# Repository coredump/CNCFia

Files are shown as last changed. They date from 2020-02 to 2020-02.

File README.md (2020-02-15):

# CNCFia

The idea with this board is to provide a *generic* shield/daughter card for 3.3V MCUs running CNC firmwares like GRBL (and its ports) and g2core. For that, instead of making a shield with specific sockets, we decided to provide a pin header that can be used to connect to different MCUs.

## Included capabilities

### Switches

There are six opto-isolated connectors for limit switches (X, Y, and Z Min/Max limits), a Probe connector and an extra opto-isolated connector to be used for any generic function, and five non-opto isolated ones to be used for external controls (Door security, Emergency Stop, etc).

The opto-isolated switches have an option to be powered by an entirely separated power source to provide full electrical isolation.

All the switches are pulled UP via 4.7kΩ resistors, intended to be used with NC (normally closed) switches connected to the GND, making it an active low signal. Take that in consideration when wiring/configuring the software.

### External driver control/level shifting

Support for nine voltage shifted outputs, mosfet (2n700X) driven. Enough to provide Step/Pulse/Enable signals for three external drivers (those usually have a 5V control voltage).

The mosfets connect the outputs to GND, so when wiring make sure to provide the 5V common wire to all positive (+) signals and the outputs to the negative (-) signals.

TODO example

## Jumper Settings

|  JP1  | Result |
| :---: | --- |
|  1-2  | 5V voltage for board functions will be provided by external power source connected to **EXTERNAL 5V IN** |
|  1-3  | 5V to board functions will be provided by the MCU 5V Pin connected to the controller input |

## Connector Descriptions

TODO add descriptions and image

## Electrical notes

View this project on [CADLAB.io](https://cadlab.io/project/2459).

All calculations were made considering a 3.3V output from the driving MCU pins, while keeping the output currents under 10 mA, what should be safe for most of the MCUs around.

The 3904s driving the relays have a base current (Ib) of ~ 7.8 mA, that should be enough to saturate the transistor and provide the 78 mA needed by the relay coil.

The LTV-847s are used with typical values for Vf and If, according to datasheet specs.

The OPAMP output for the spindle can be regulated with a potentiometer and from the 3.3V PWM it can get values close to 11V with a 12V power source. Simulated circuit shows a 0.4s approximately time to get to the stable voltage.

## License, Copyright and disclaimers

Copyright Jose Junior <jose.junior@gmail.com> 2020.  

This documentation describes Open Hardware and is licensed under the
CERN OHL v. 1.2.  

You may redistribute and modify this documentation under the terms of the
[CERN OHL v.1.2.](http://ohwr.org/cernohl) This documentation is distributed
**WITHOUT ANY EXPRESS OR IMPLIED WARRANTY, INCLUDING OF
MERCHANTABILITY, SATISFACTORY QUALITY AND FITNESS FOR A
PARTICULAR PURPOSE**. Please see the CERN OHL v.1.2 for applicable
conditions.

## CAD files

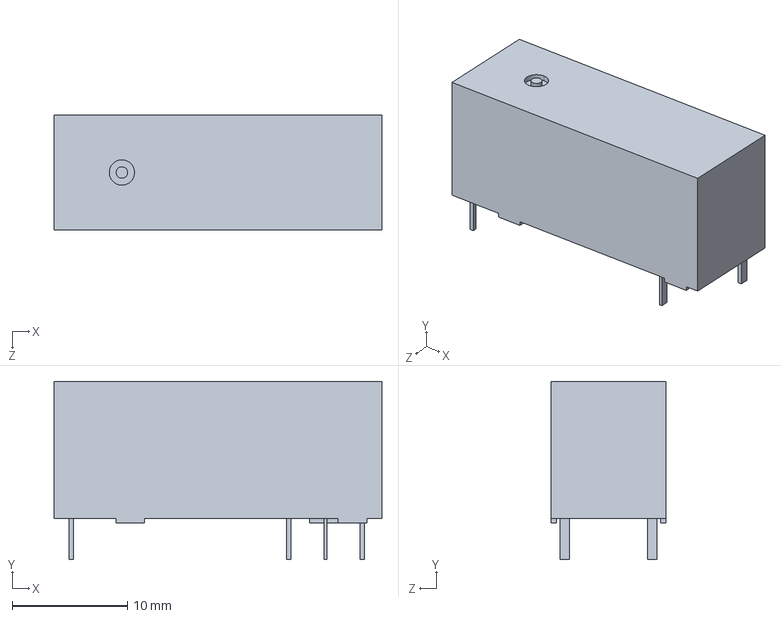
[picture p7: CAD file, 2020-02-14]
Custom/Kicad_extra_3d/G6RL_1.step
28.5 x 15.5 x 10.0 mm

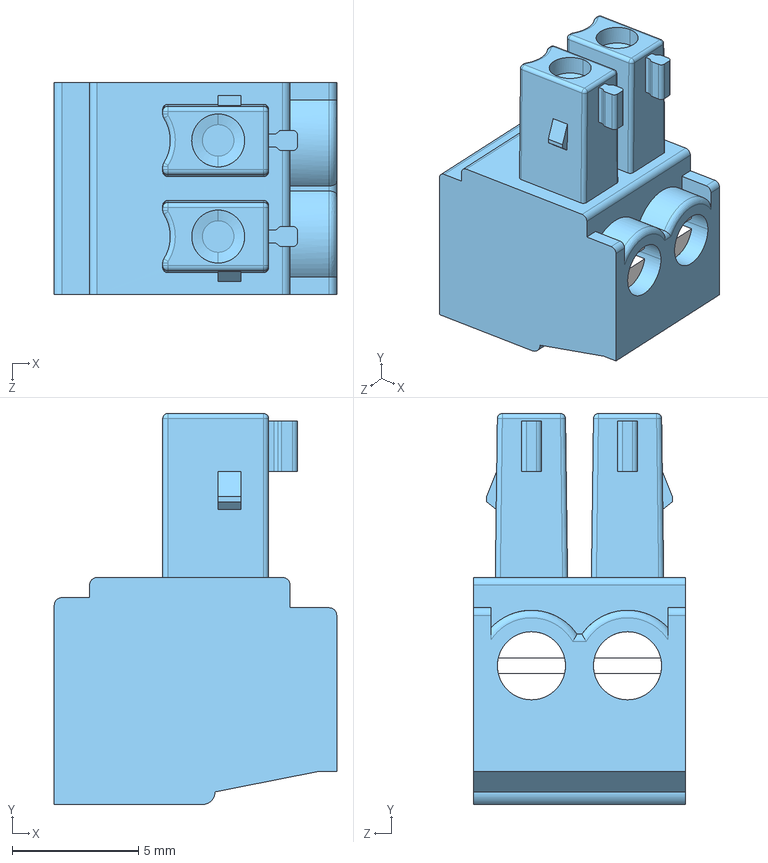
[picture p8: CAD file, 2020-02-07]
Custom/Kicad_extra_3d/CUI_DEVICES_TBP02P1-381-02BE.step
11.2 x 15.5 x 8.41 mm

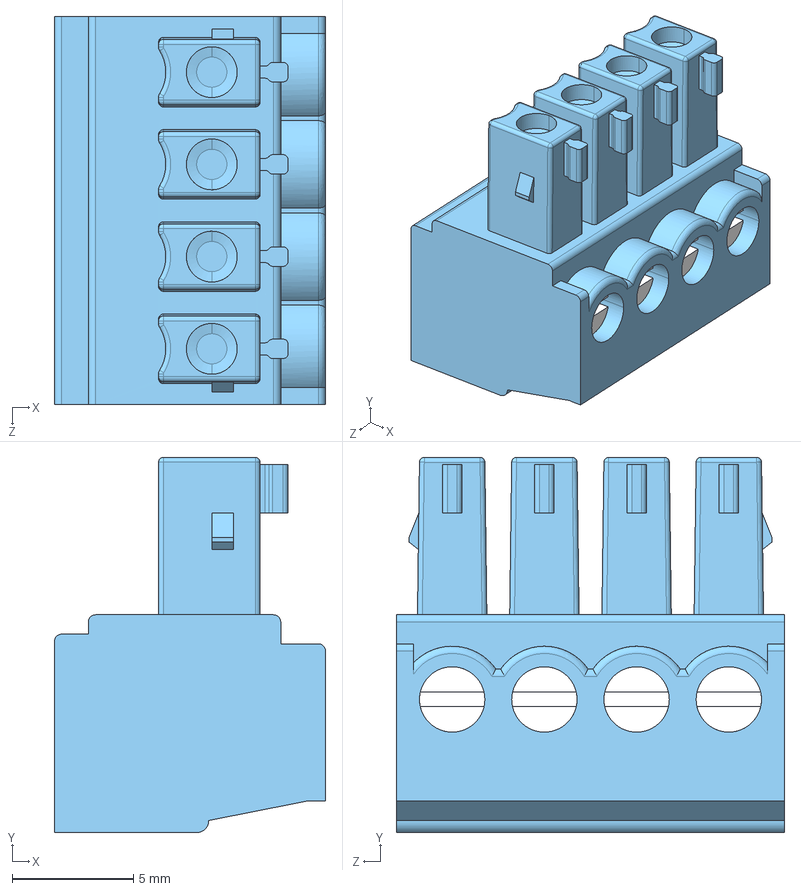
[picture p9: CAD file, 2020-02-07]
Custom/Kicad_extra_3d/CUI_DEVICES_TBP02P1-381-04BE.step
11.2 x 15.5 x 16.0 mm

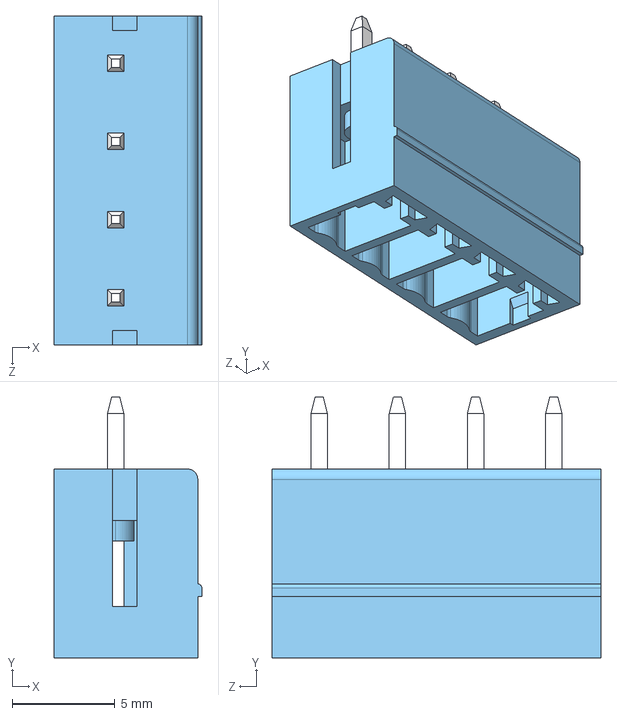
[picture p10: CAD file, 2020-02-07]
Custom/Kicad_extra_3d/CUI_DEVICES_TBP02R2-381-04BE.step
7.20 x 12.7 x 16.0 mm

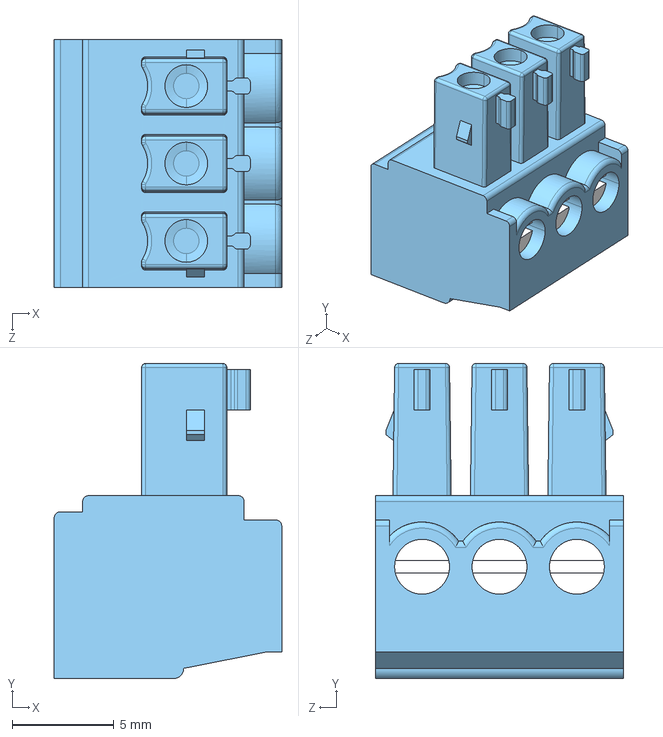
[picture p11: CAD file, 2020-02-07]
Custom/Kicad_extra_3d/CUI_DEVICES_TBP02P1-381-03BE.step
11.2 x 15.5 x 12.2 mm

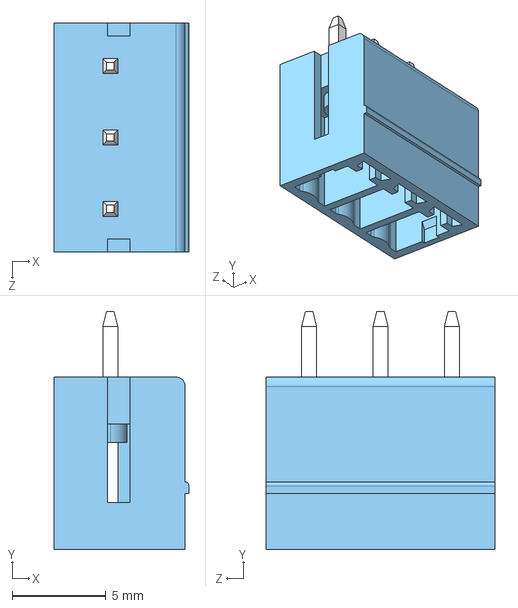
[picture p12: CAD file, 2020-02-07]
Custom/Kicad_extra_3d/CUI_DEVICES_TBP02R2-381-03BE.step
7.20 x 12.7 x 12.2 mm

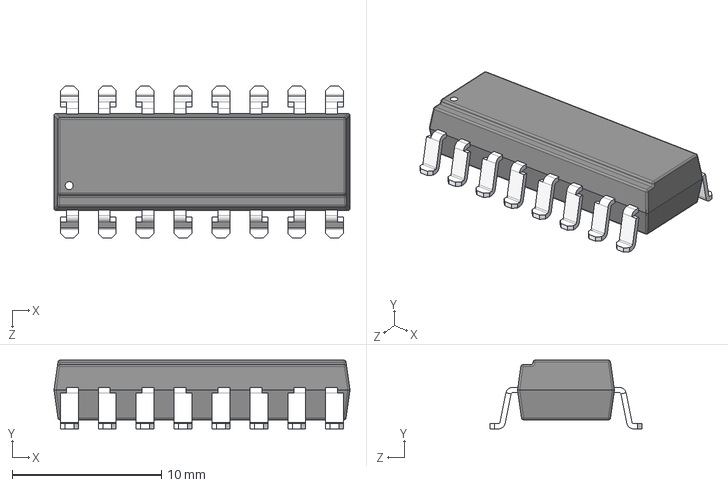
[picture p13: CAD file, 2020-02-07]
Custom/Kicad_extra_3d/LTV-846S--3DModel-STEP-56544.STEP
19.8 x 4.60 x 10.2 mm

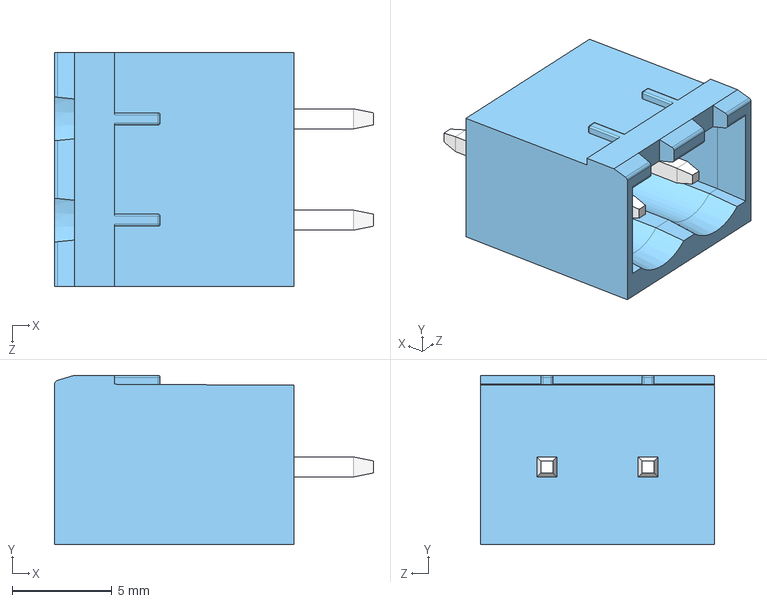
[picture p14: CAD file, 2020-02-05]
Custom/Kicad_extra_3d/CUI_DEVICES_TBP01R2-508-02BE.step
16.0 x 8.50 x 11.8 mm

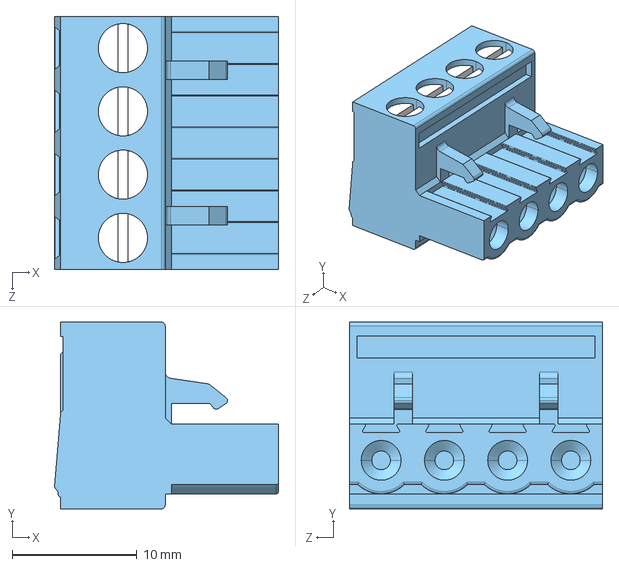
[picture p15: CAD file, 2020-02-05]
Custom/Kicad_extra_3d/CUI_DEVICES_TBP01P1-508-04BE.step
18.0 x 15.0 x 20.3 mm

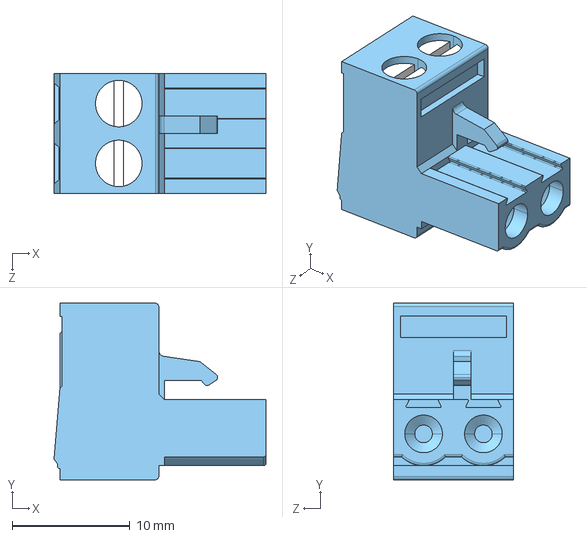
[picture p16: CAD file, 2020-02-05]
Custom/Kicad_extra_3d/CUI_DEVICES_TBP01P1-508-02BE.step
18.0 x 15.0 x 10.2 mm

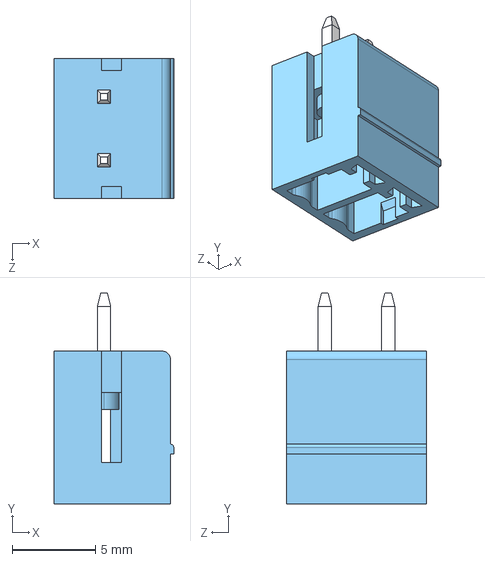
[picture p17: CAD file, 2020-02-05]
Custom/Kicad_extra_3d/CUI_DEVICES_TBP02R2-381-02BE.step
7.20 x 12.7 x 8.41 mm

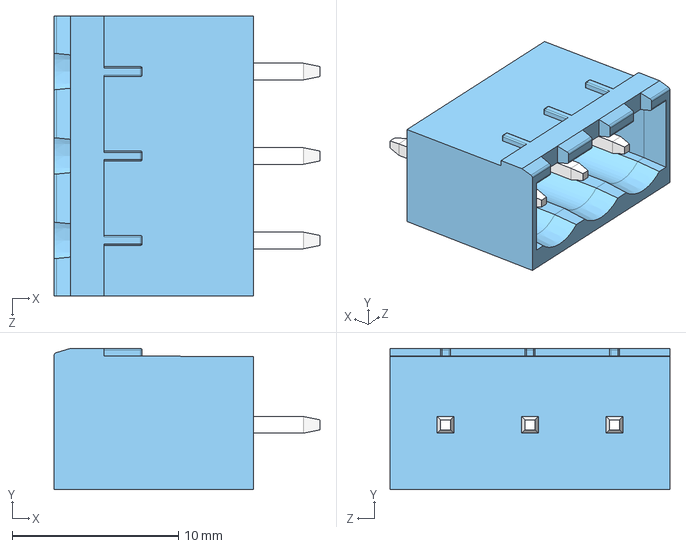
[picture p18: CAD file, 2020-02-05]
Custom/Kicad_extra_3d/CUI_DEVICES_TBP01R2-508-03BE.step
16.0 x 8.50 x 16.8 mm

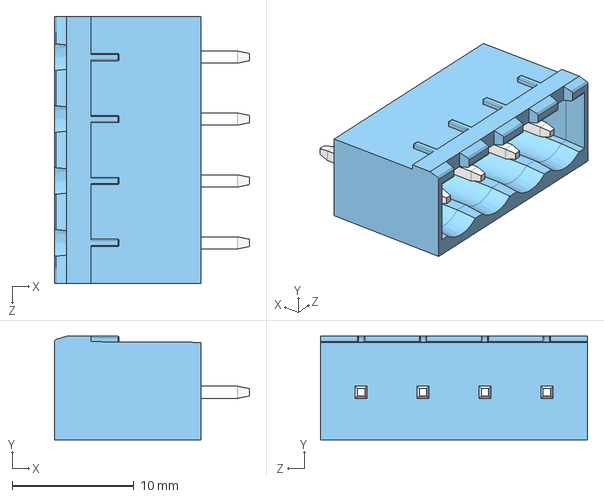
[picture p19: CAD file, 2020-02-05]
Custom/Kicad_extra_3d/CUI_DEVICES_TBP01R2-508-04BE.step
16.0 x 8.50 x 21.9 mm

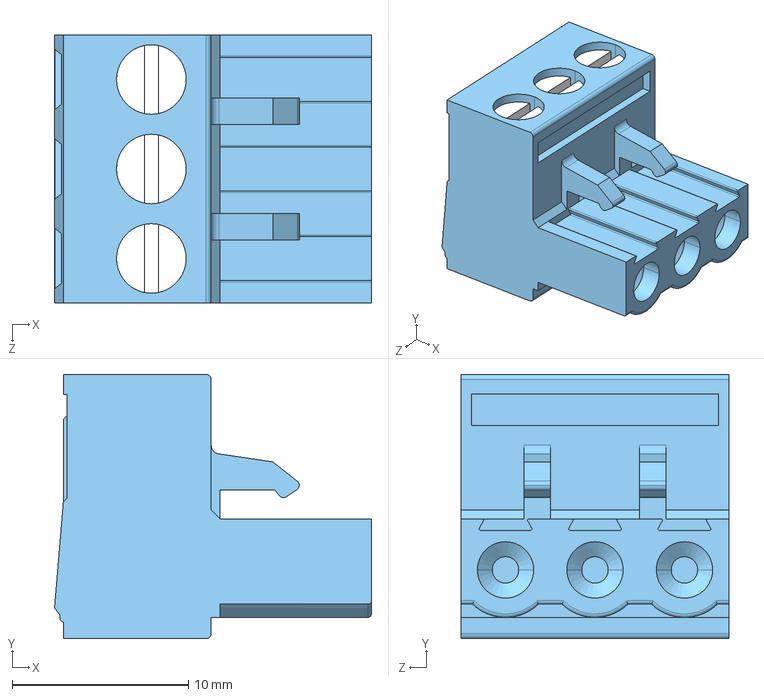
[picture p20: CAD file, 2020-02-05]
Custom/Kicad_extra_3d/CUI_DEVICES_TBP01P1-508-03BE.step
18.0 x 15.0 x 15.2 mm

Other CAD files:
Custom/Kicad_extra_3d/Omron Single.stp

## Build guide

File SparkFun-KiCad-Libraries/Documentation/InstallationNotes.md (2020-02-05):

Installation Notes
----------------

* [The KiCad site](http://kicad-pcb.org/)

**KiCad installation**

* Uninstall previous versions of KiCad
* Download KiCad stable version 4.0.5 from [http://kicad-pcb.org/download/](http://kicad-pcb.org/download/windows/) and install
* After install, you'll be prompted to install "Wings 3D", check this box to be redirected to [http://www.wings3d.com/](http://www.wings3d.com/)
* Download and install the stable release 2.1.5

**Using the libraries**

* Create a local project (this is necessary because projects hold library path information)
* Open the "Schematic Library Editor"
* Prefrences -> Component Libraries
  * Remove all libraries from list
  * Add -> navigate to SparkFun-KiCad-Libraries -> select all .lib files -> open, then hit OK
  * Test by selecting an active library.  All sparkfun libraries should be displayed.  Close the library editor
* Open the "PCB Footprint Editor"
* Preferences -> Footprint Library Manager
  * Remove all (if any) libraries, hit OK
* Preferences -> Footprint Libraries Wizard
  * Next (files on my computer)
  * Navigate to SparkFun-KiCad-Libraries -> select all .mod files and hit ok
  * Next
  * Select for this project only
  * Next
  * Close the editor
* Save the project (Green arrow into extern HDD icon, no menu exists)

Now, this project is linked to the libraries.  Open a schematic and place components.  See KiCad enginursday post for converting from schematic into board (Note: You need to have nets for this to work... not just unconnected components)

**License Information**

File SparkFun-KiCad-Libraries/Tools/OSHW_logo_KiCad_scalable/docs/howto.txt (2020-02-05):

How to make your own:
---------------------

Watch / read this first:

* http://www.kicad-pcb.org/display/KICAD/Videos+by+zupnikal

The last two videos should be helpful for how to create a custom .emp file from images.

* http://www.re-innovation.co.uk/web12/index.php/en/blog-75/230-adding-logo-to-kicad

If you use linux (which you should), you don't have to use the online-scaler. Just use the scripts!

---

* Create a folder to hold your new footprint library.
* Copy the scripts 'make_lib.sh' and 'scale.pl' into that folder.
* Make sure these files are executable (chmod u+x ...).
* Copy your custom .emp file into that foler.

* Run the 'make_lib.sh' script as follows:

./make_lib.sh input-file.emp lib-name.mod START END

START and END are placeholders for positive integer numbers (1,2,3...) that determine
the range of created footprint sizes. The units are metric (mm).

The 'lib-name.mod' file will show up in the 'lib' sub-folder. Add it to your pcbnew
library settings as usual.

Footprints that are created for back-layers are automagically mirrored horizontally.
To place them onto a back-layer, hover the mouse-pointer over them and press 'f' for 'flip'.

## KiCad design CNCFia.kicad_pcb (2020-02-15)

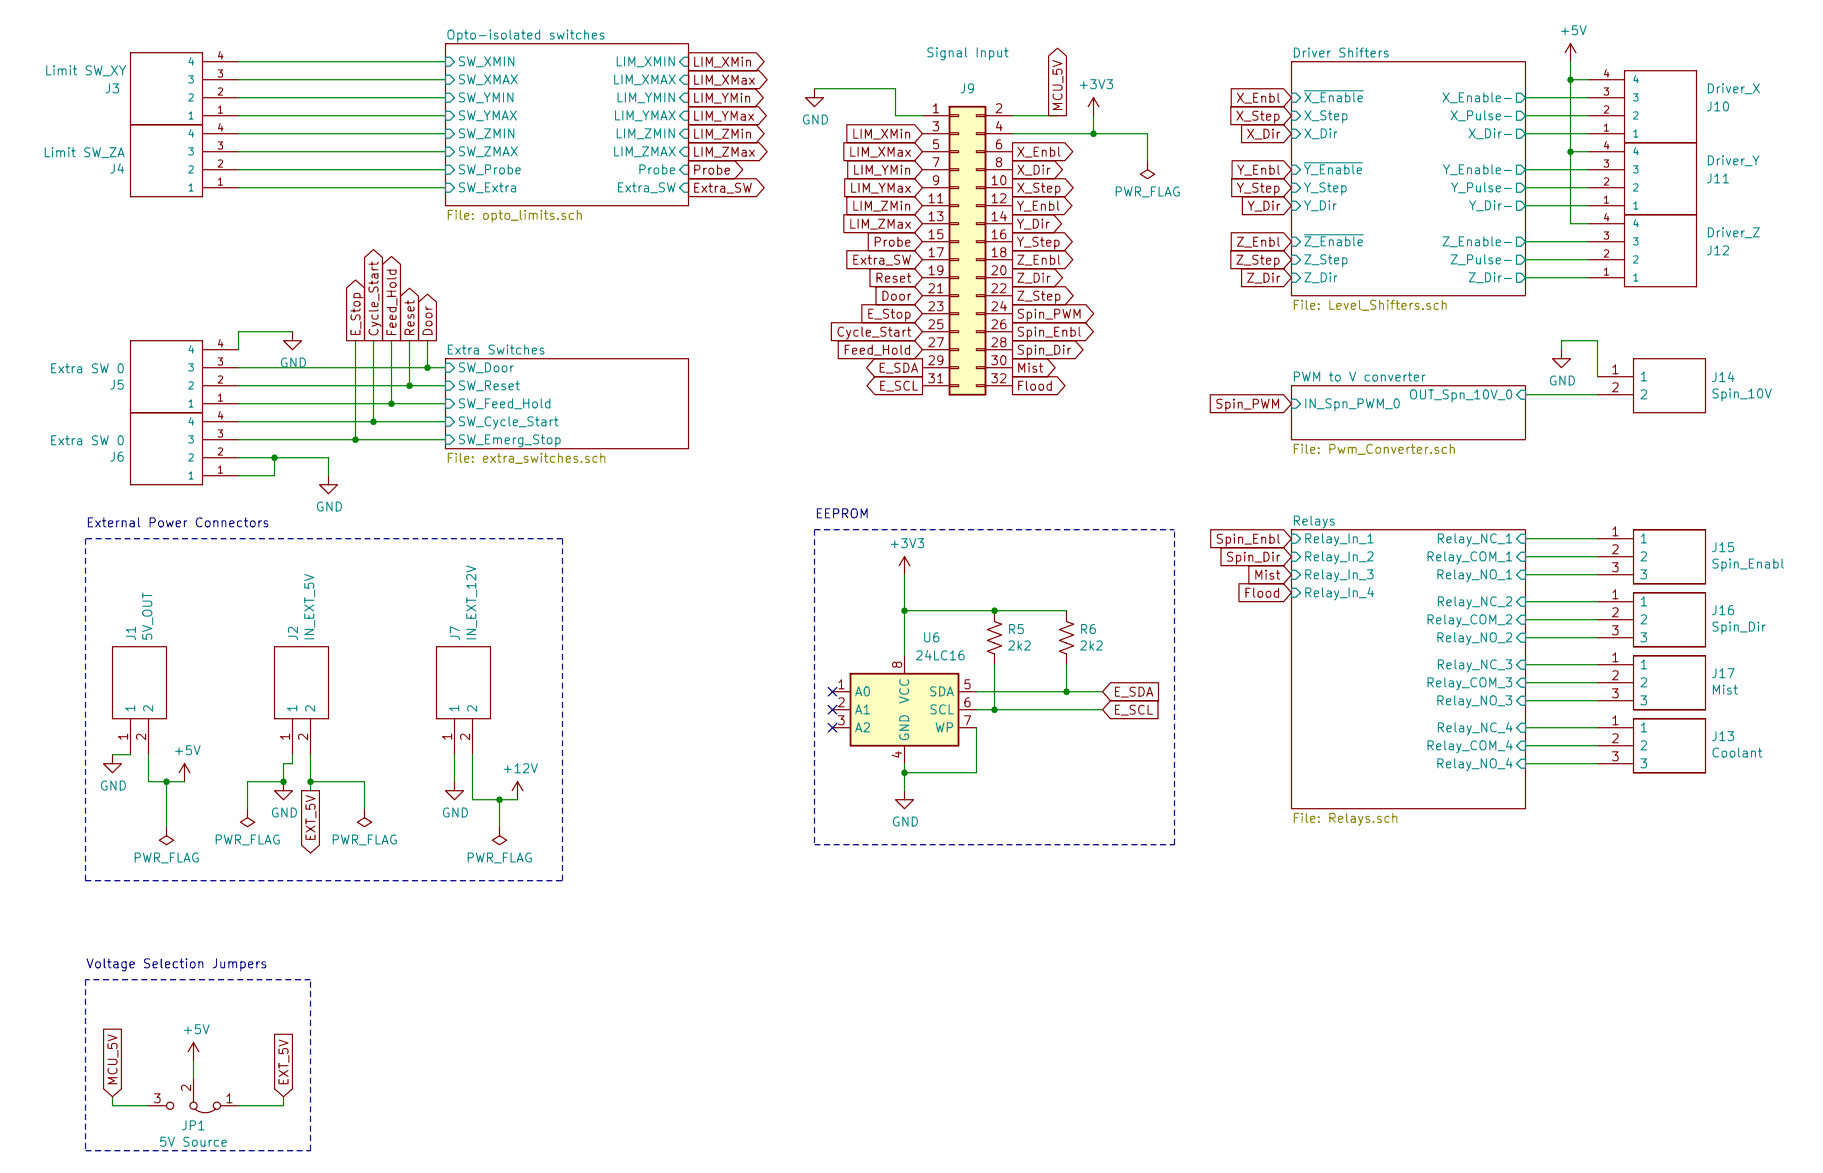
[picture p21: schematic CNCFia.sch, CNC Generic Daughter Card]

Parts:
J1: 5V_OUT; CUI_TBP02R2-381-02BE; Mouser Part Number 490-TB008A-508-02BE
J2: IN_EXT_5V; CUI_TBP02R2-381-02BE; Mouser Part Number 490-TB008A-508-02BE
J3: Limit SW_XY; CUI_TBP02R2-381-04BE; MPN TBP01R2-508-04BE; Digi-Key_PN 102-6424-ND
J4: Limit SW_ZA; CUI_TBP02R2-381-04BE; MPN TBP01R2-508-04BE; Digi-Key_PN 102-6424-ND
J5, J6: Extra SW 0; CUI_TBP02R2-381-04BE; MPN TBP01R2-508-04BE; Digi-Key_PN 102-6424-ND
J7: IN_EXT_12V; CUI_TBP02R2-381-02BE; Mouser Part Number 490-TB008A-508-02BE
J9: Signal Input; PinHeader_2x16_P2.54mm_Vertical; MPN 302-S401; Digi-Key_PN ED10529-ND
J10: Driver_X; CUI_TBP02R2-381-04BE; Mouser Part Number 490-TB008A-508-03BE
J11: Driver_Y; CUI_TBP02R2-381-04BE; Mouser Part Number 490-TB008A-508-03BE
J12: Driver_Z; CUI_TBP02R2-381-04BE; Mouser Part Number 490-TB008A-508-03BE
J13: Coolant; CUI_TBP02R2-381-03BE; Mouser Part Number 490-TB008A-508-03BE
J14: Spin_10V; CUI_TBP02R2-381-02BE; Mouser Part Number 490-TB008A-508-02BE
J15: Spin_Enabl; CUI_TBP02R2-381-03BE; Mouser Part Number 490-TB008A-508-03BE
J16: Spin_Dir; CUI_TBP02R2-381-03BE; Mouser Part Number 490-TB008A-508-03BE
J17: Mist; CUI_TBP02R2-381-03BE; Mouser Part Number 490-TB008A-508-03BE
JP1: 5V Source; PinHeader_1x03_P2.54mm_Vertical
R5, R6: 2k2; R_0805_2012Metric_Pad1.15x1.40mm_HandSolder; MPN CRGCQ1206F2K2; Digi-Key_PN A129814CT-ND
U6: 24LC16; SOIC-8_3.9x4.9mm_P1.27mm

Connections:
+3V3: J9.4, R5.1, R6.1, U6.8 (VCC); also elsewhere on the board
+5V: J1.2, J10.4, J11.4, J12.4, JP1.2 (C); also elsewhere on the board
+12V: J7.2; also elsewhere on the board
/OUT_Spn_10V_0: J14.2; also elsewhere on the board
/Relay_COM_1: J15.2; also elsewhere on the board
/Relay_COM_2: J16.2; also elsewhere on the board
/Relay_COM_3: J17.2; also elsewhere on the board
/Relay_COM_4: J13.2; also elsewhere on the board
/Relay_NC_1: J15.1; also elsewhere on the board
/Relay_NC_2: J16.1; also elsewhere on the board
/Relay_NC_3: J17.1; also elsewhere on the board
/Relay_NC_4: J13.1; also elsewhere on the board
/Relay_NO_1: J15.3; also elsewhere on the board
/Relay_NO_2: J16.3; also elsewhere on the board
/Relay_NO_3: J17.3; also elsewhere on the board
/Relay_NO_4: J13.3; also elsewhere on the board
/SW_Extra: J4.1; also elsewhere on the board
/SW_Probe: J4.2; also elsewhere on the board
/SW_XMAX: J3.3; also elsewhere on the board
/SW_XMIN: J3.4; also elsewhere on the board
/SW_YMAX: J3.1; also elsewhere on the board
/SW_YMIN: J3.2; also elsewhere on the board
/SW_ZMAX: J4.3; also elsewhere on the board
/SW_ZMIN: J4.4; also elsewhere on the board
/X_Dir-: J10.1; also elsewhere on the board
/X_Enable-: J10.3; also elsewhere on the board
/X_Pulse-: J10.2; also elsewhere on the board
/Y_Dir-: J11.1; also elsewhere on the board
/Y_Enable-: J11.3; also elsewhere on the board
/Y_Pulse-: J11.2; also elsewhere on the board
/Z_Dir-: J12.1; also elsewhere on the board
/Z_Enable-: J12.3; also elsewhere on the board
/Z_Pulse-: J12.2; also elsewhere on the board
Cycle_Start: J6.4, J9.25; also elsewhere on the board
Door: J5.3, J9.21; also elsewhere on the board
EXT_5V: J2.2, JP1.1 (A)
E_SCL: J9.31, R5.2, U6.6 (SCL)
E_SDA: J9.29, R6.2, U6.5 (SDA)
E_Stop: J6.3, J9.23; also elsewhere on the board
Extra_SW: J9.17; also elsewhere on the board
Feed_Hold: J5.1, J9.27; also elsewhere on the board
Flood: J9.32; also elsewhere on the board
GND: J1.1, J2.1, J5.4, J6.1, J6.2, J7.1, J9.1, J14.1, U6.4 (GND), U6.7 (WP); also elsewhere on the board
LIM_XMax: J9.5; also elsewhere on the board
LIM_XMin: J9.3; also elsewhere on the board
LIM_YMax: J9.9; also elsewhere on the board
LIM_YMin: J9.7; also elsewhere on the board
LIM_ZMax: J9.13; also elsewhere on the board
LIM_ZMin: J9.11; also elsewhere on the board
MCU_5V: J9.2, JP1.3 (B)
Mist: J9.30; also elsewhere on the board
Probe: J9.15; also elsewhere on the board
Reset: J5.2, J9.19; also elsewhere on the board
Spin_Dir: J9.28; also elsewhere on the board
Spin_Enbl: J9.26; also elsewhere on the board
Spin_PWM: J9.24; also elsewhere on the board
X_Dir: J9.8; also elsewhere on the board
X_Enbl: J9.6; also elsewhere on the board
X_Step: J9.10; also elsewhere on the board
Y_Dir: J9.14; also elsewhere on the board
Y_Enbl: J9.12; also elsewhere on the board
Y_Step: J9.16; also elsewhere on the board
Z_Dir: J9.20; also elsewhere on the board
Z_Enbl: J9.18; also elsewhere on the board
Z_Step: J9.22; also elsewhere on the board

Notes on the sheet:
External Power Connectors
Voltage Selection Jumpers
EEPROM

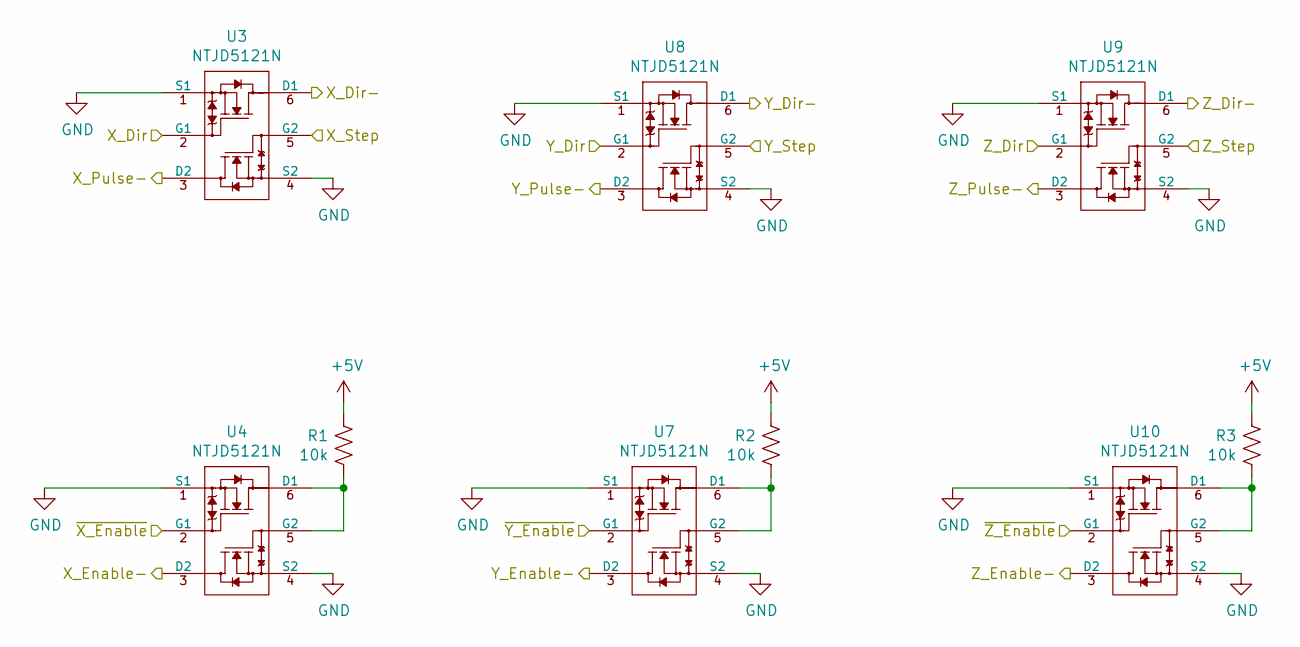
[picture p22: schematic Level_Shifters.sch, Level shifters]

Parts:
R1, R2, R3: 10k; R_0805_2012Metric_Pad1.15x1.40mm_HandSolder
U3, U4, U7, U8, U9, U10: NTJD5121N; SOT-363_SC-70-6

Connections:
+5V: R1.1, R2.1, R3.1; also elsewhere on the board
/X_Dir-: U3.6 (D1); also elsewhere on the board
/X_Enable-: U4.3 (D2); also elsewhere on the board
/X_Pulse-: U3.3 (D2); also elsewhere on the board
/Y_Dir-: U8.6 (D1); also elsewhere on the board
/Y_Enable-: U7.3 (D2); also elsewhere on the board
/Y_Pulse-: U8.3 (D2); also elsewhere on the board
/Z_Dir-: U9.6 (D1); also elsewhere on the board
/Z_Enable-: U10.3 (D2); also elsewhere on the board
/Z_Pulse-: U9.3 (D2); also elsewhere on the board
GND: U3.1 (S1), U3.4 (S2), U4.1 (S1), U4.4 (S2), U7.1 (S1), U7.4 (S2), U8.1 (S1), U8.4 (S2), U9.1 (S1), U9.4 (S2), U10.1 (S1), U10.4 (S2); also elsewhere on the board
unnamed: R1.2, U4.5 (G2), U4.6 (D1)
unnamed: R2.2, U7.5 (G2), U7.6 (D1)
unnamed: R3.2, U10.5 (G2), U10.6 (D1)
X_Dir: U3.2 (G1); also elsewhere on the board
X_Enbl: U4.2 (G1); also elsewhere on the board
X_Step: U3.5 (G2); also elsewhere on the board
Y_Dir: U8.2 (G1); also elsewhere on the board
Y_Enbl: U7.2 (G1); also elsewhere on the board
Y_Step: U8.5 (G2); also elsewhere on the board
Z_Dir: U9.2 (G1); also elsewhere on the board
Z_Enbl: U10.2 (G1); also elsewhere on the board
Z_Step: U9.5 (G2); also elsewhere on the board

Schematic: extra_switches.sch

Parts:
RN3: CAY17-472JALF; RESCAXS64P320X160X60-10N; MPN CAY17-472JALF; Digi-Key_PN CAY17-472JALFCT-ND

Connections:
+3V3: RN3.5, RN3.10; also elsewhere on the board
Cycle_Start: RN3.2; also elsewhere on the board
Door: RN3.6; also elsewhere on the board
E_Stop: RN3.1; also elsewhere on the board
Feed_Hold: RN3.3; also elsewhere on the board
Reset: RN3.4; also elsewhere on the board

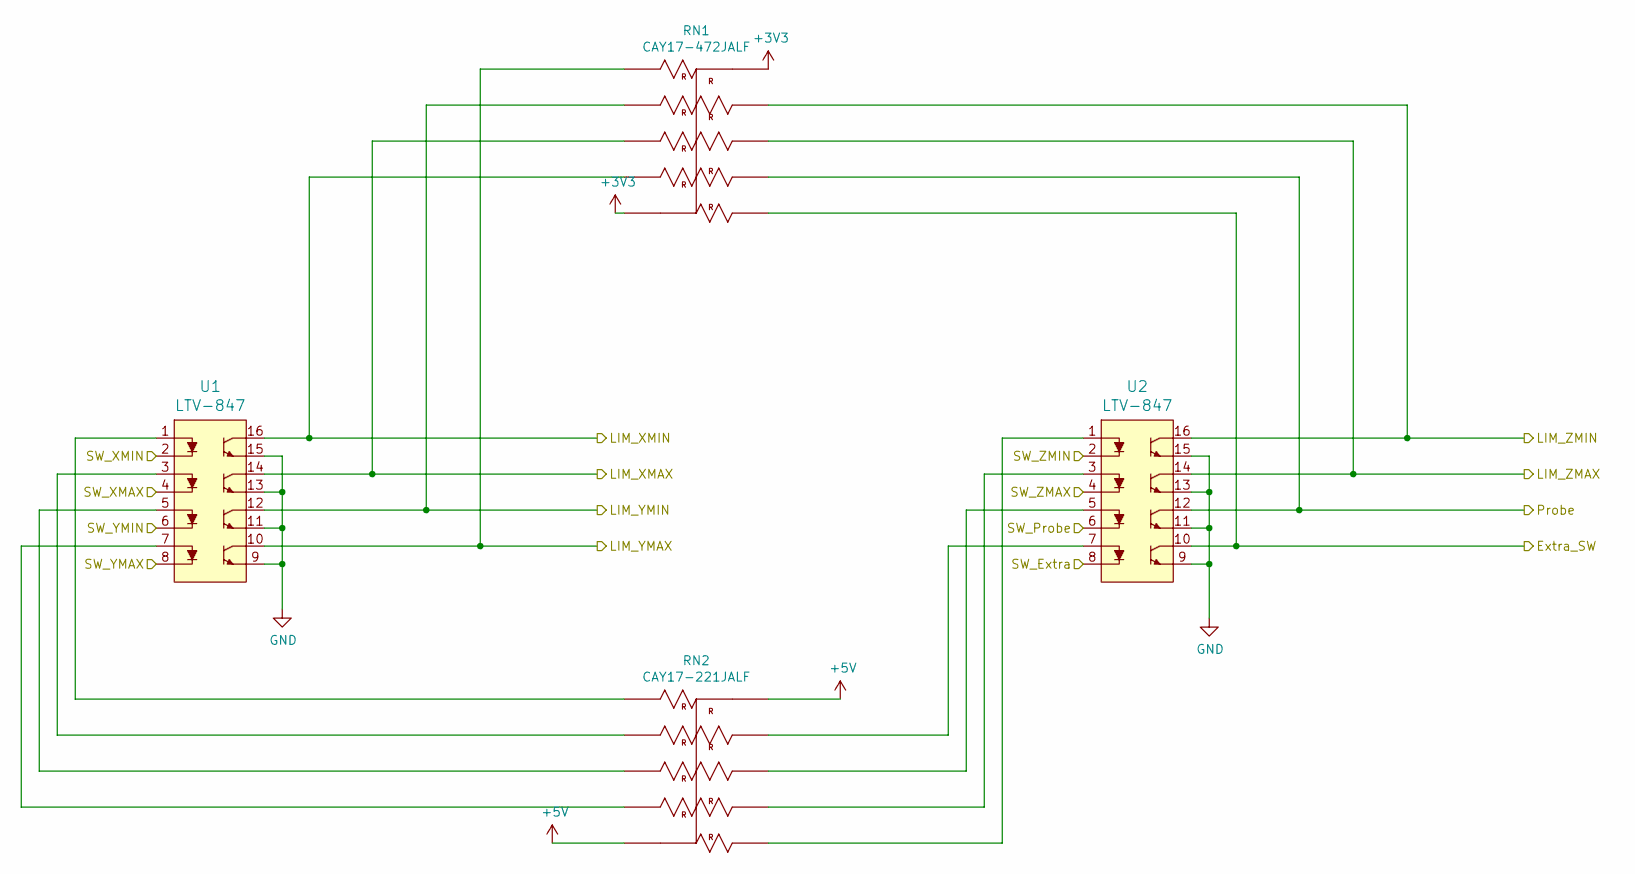
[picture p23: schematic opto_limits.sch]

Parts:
RN1: CAY17-472JALF; RESCAXS64P320X160X60-10N; MPN CAY17-472JALF; Digi-Key_PN CAY17-472JALFCT-ND
RN2: CAY17-221JALF; RESCAXS64P320X160X60-10N; MPN CAY17-221JALF; Digi-Key_PN CAY17-221JALF-ND
U1, U2: LTV-847; SOIC254P1016X460-16N; MPN LTV-847S; Digi-Key_PN 160-1371-5-ND

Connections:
+3V3: RN1.5, RN1.10; also elsewhere on the board
+5V: RN2.5, RN2.10; also elsewhere on the board
/SW_Extra: U2.8; also elsewhere on the board
/SW_Probe: U2.6; also elsewhere on the board
/SW_XMAX: U1.4; also elsewhere on the board
/SW_XMIN: U1.2; also elsewhere on the board
/SW_YMAX: U1.8; also elsewhere on the board
/SW_YMIN: U1.6; also elsewhere on the board
/SW_ZMAX: U2.4; also elsewhere on the board
/SW_ZMIN: U2.2; also elsewhere on the board
Extra_SW: RN1.1, U2.10; also elsewhere on the board
GND: U1.9, U1.11, U1.13, U1.15, U2.9, U2.11, U2.13, U2.15; also elsewhere on the board
LIM_XMax: RN1.8, U1.14; also elsewhere on the board
LIM_XMin: RN1.9, U1.16; also elsewhere on the board
LIM_YMax: RN1.6, U1.10; also elsewhere on the board
LIM_YMin: RN1.7, U1.12; also elsewhere on the board
LIM_ZMax: RN1.3, U2.14; also elsewhere on the board
LIM_ZMin: RN1.4, U2.16; also elsewhere on the board
unnamed: RN2.1, U2.1
unnamed: RN2.2, U2.3
unnamed: RN2.3, U2.5
unnamed: RN2.4, U2.7
unnamed: RN2.6, U1.1
unnamed: RN2.7, U1.3
unnamed: RN2.8, U1.5
unnamed: RN2.9, U1.7
Probe: RN1.2, U2.12; also elsewhere on the board

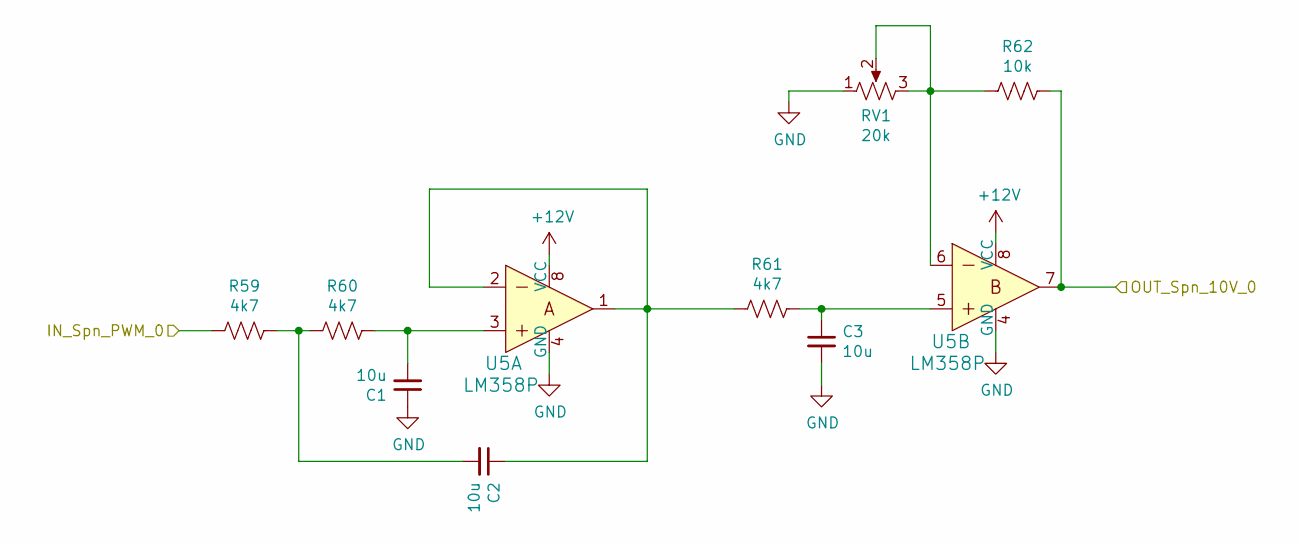
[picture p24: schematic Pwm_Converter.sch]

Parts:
C1, C2, C3: 10u; C_1206_3216Metric_Pad1.42x1.75mm_HandSolder; MPN CL31A106MQHNNNE; Digi-Key_PN 1276-3045-1-ND
R59, R60, R61: 4k7; R_0805_2012Metric_Pad1.15x1.40mm_HandSolder; MPN CRGCQ1206F4K7; Digi-Key_PN A129818CT-ND
R62: 10k; R_0805_2012Metric_Pad1.15x1.40mm_HandSolder; MPN CRGCQ1206J10K; Digi-Key_PN A130183CT-ND
RV1: 20k; Potentiometer_ACP_CA6-H2,5_Horizontal; MPN N6L50T0C-203; Digi-Key_PN 1993-1217-ND
U5: LM358P; SOIC-8_3.9x4.9mm_P1.27mm; MPN LM358ADRG4; Digi-Key_PN 296-31667-1-ND

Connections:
+12V: U5.8 (VCC); also elsewhere on the board
/OUT_Spn_10V_0: R62.1, U5.7; also elsewhere on the board
GND: C1.1, C3.2, RV1.1, U5.4 (GND); also elsewhere on the board
unnamed: C1.2, R60.1, U5.3
unnamed: C2.1, R61.2, U5.1, U5.2
unnamed: C2.2, R59.1, R60.2
unnamed: C3.1, R61.1, U5.5
unnamed: R62.2, RV1.2, RV1.3, U5.6
Spin_PWM: R59.2; also elsewhere on the board

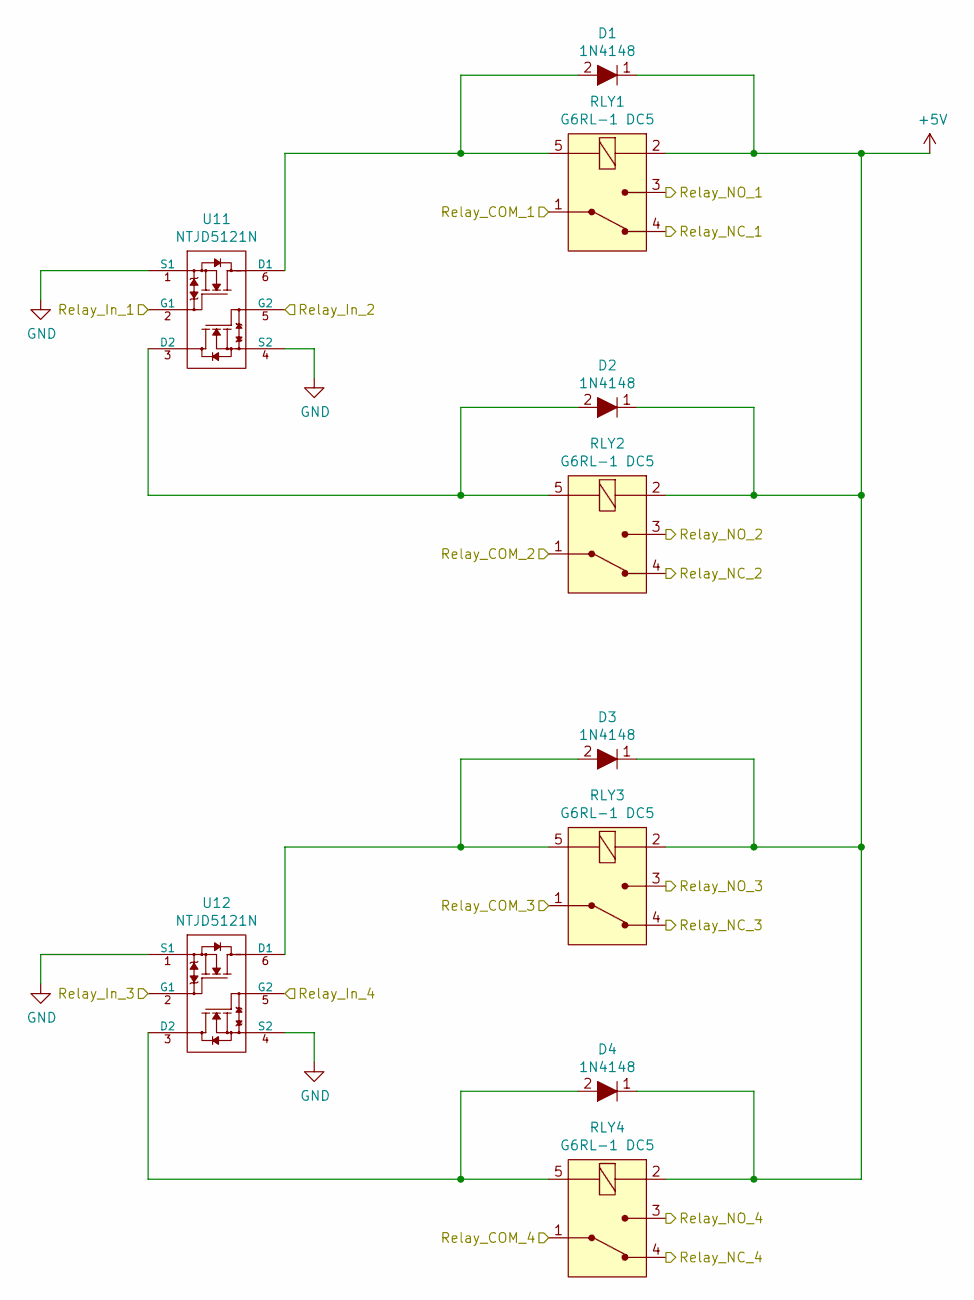
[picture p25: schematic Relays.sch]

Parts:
D1, D2, D3, D4: 1N4148; D_SOD-123; MPN MMSD4148T1G; Digi-Key_PN MMSD4148T1GOSCT-ND
RLY1, RLY2, RLY3, RLY4: G6RL-1 DC5; RELAY_G6RL-1_5VDC; MPN G6RL-1 DC5; Digi-Key_PN Z2902-ND
U11, U12: NTJD5121N; SOT-363_SC-70-6

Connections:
+5V: D1.1, D2.1, D3.1, D4.1, RLY1.2 (COIL), RLY2.2 (COIL), RLY3.2 (COIL), RLY4.2 (COIL); also elsewhere on the board
/Relay_COM_1: RLY1.1 (COM); also elsewhere on the board
/Relay_COM_2: RLY2.1 (COM); also elsewhere on the board
/Relay_COM_3: RLY3.1 (COM); also elsewhere on the board
/Relay_COM_4: RLY4.1 (COM); also elsewhere on the board
/Relay_NC_1: RLY1.4 (NC); also elsewhere on the board
/Relay_NC_2: RLY2.4 (NC); also elsewhere on the board
/Relay_NC_3: RLY3.4 (NC); also elsewhere on the board
/Relay_NC_4: RLY4.4 (NC); also elsewhere on the board
/Relay_NO_1: RLY1.3 (NO); also elsewhere on the board
/Relay_NO_2: RLY2.3 (NO); also elsewhere on the board
/Relay_NO_3: RLY3.3 (NO); also elsewhere on the board
/Relay_NO_4: RLY4.3 (NO); also elsewhere on the board
Flood: U12.5 (G2); also elsewhere on the board
GND: U11.1 (S1), U11.4 (S2), U12.1 (S1), U12.4 (S2); also elsewhere on the board
Mist: U12.2 (G1); also elsewhere on the board
unnamed: D1.2, RLY1.5 (COIL), U11.6 (D1)
unnamed: D2.2, RLY2.5 (COIL), U11.3 (D2)
unnamed: D3.2, RLY3.5 (COIL), U12.6 (D1)
unnamed: D4.2, RLY4.5 (COIL), U12.3 (D2)
Spin_Dir: U11.5 (G2); also elsewhere on the board
Spin_Enbl: U11.2 (G1); also elsewhere on the board

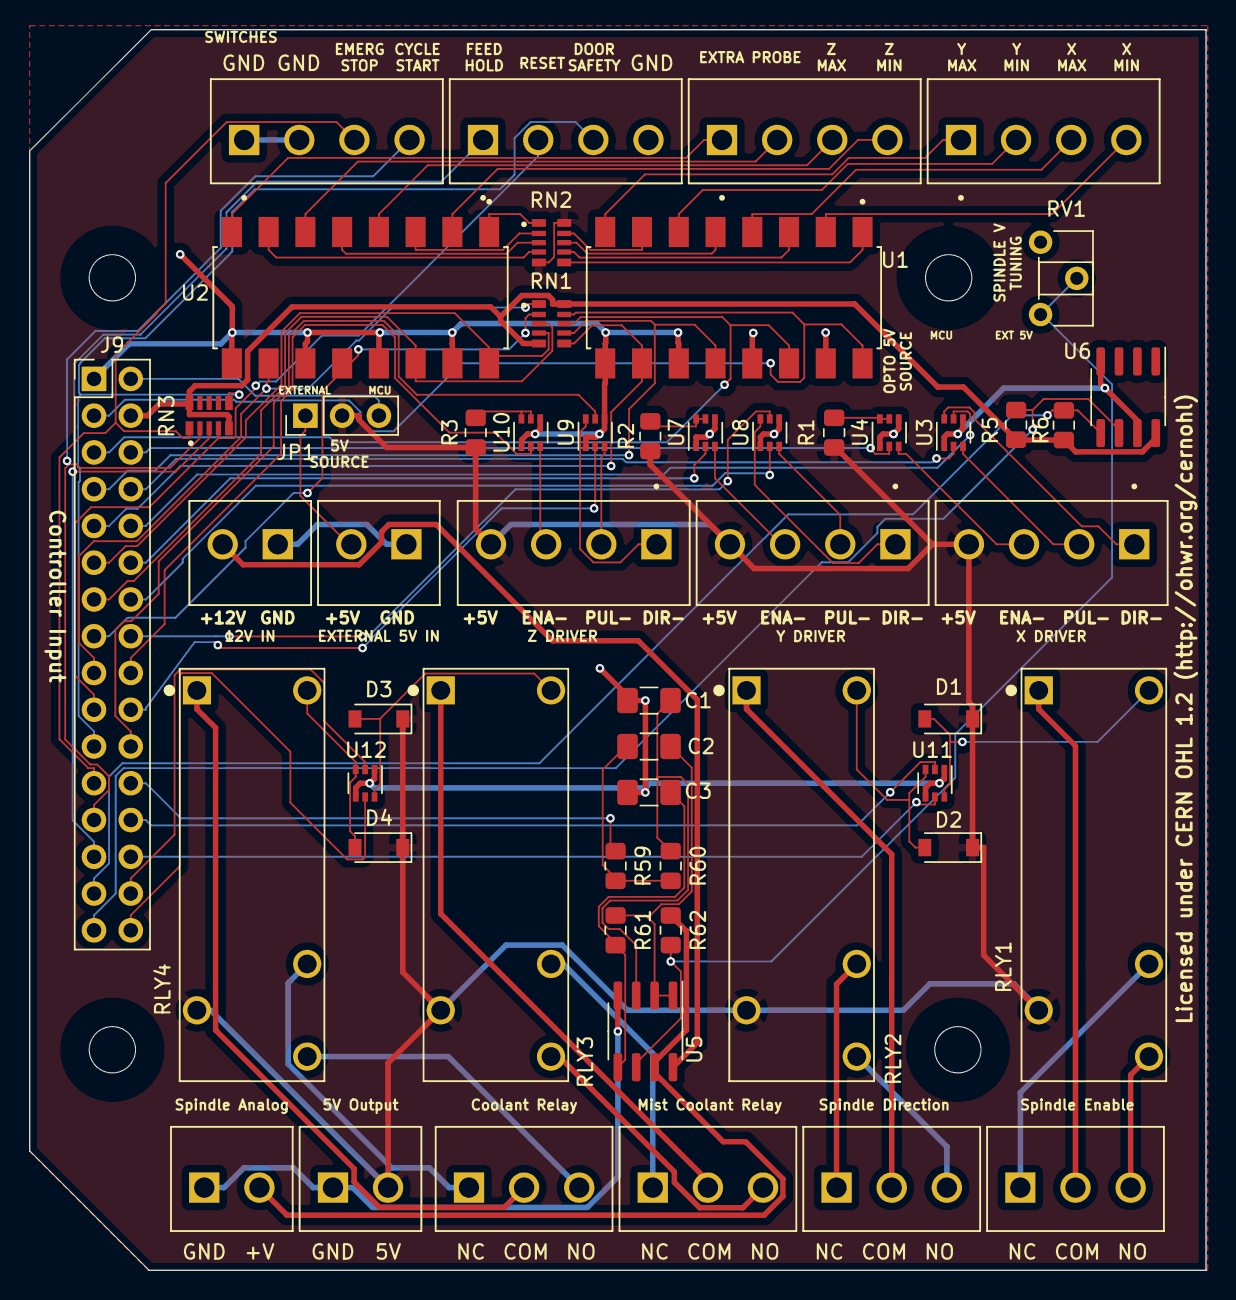
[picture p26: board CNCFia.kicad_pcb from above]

Board: 2 copper layers, 81.3 x 85.7 mm, 57 parts (0 on the bottom side), 85 nets.

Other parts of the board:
M1, M2, M3, M4: MountingHole_3.2mm_M3

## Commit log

2020-02-05 Renamed Kicad Project, cleanup
    [CNCFia.kicad_pcb, CNCFia.sch, CNC_generic_adapter.kicad_pcb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]
2020-02-05 Flatten submodules into repo
    [boostboard1-B.Cu.gbr, boostboard1-B.Mask.gbr, boostboard1-B.Paste.gbr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]
2020-02-05 Even more flattening for Cadlab
    [CUI_DEVICES_TBP01P1-508-02BE.step, CUI_DEVICES_TBP01P1-508-03BE.step, CUI_DEVICES_TBP01P1-508-04BE.step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]
2020-02-05 Remove extraneous Sparkfun stuff
    [boostboard1-B.Cu.gbr, boostboard1-B.Mask.gbr, boostboard1-B.Paste.gbr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]
2020-02-05 Before autorouting
    [CNCFia.kicad_pcb]
2020-02-07 Makes it SMD based, with smaller connectors
    [CNCFia.kicad_pcb, CNCFia.sch, CUI_DEVICES_TBP02P1-381-02BE.step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]
2020-02-07 Vertical mounted version
    [CNCFia.kicad_pcb, CNCFia.sch]
2020-02-07 New routing
    [CNCFia.kicad_pcb]
2020-02-07 Fixing schematic symbols
    [CNCFia.kicad_pcb, CNCFia.sch, Pwm_Converter.sch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]
2020-02-07 Added some more comments to sheets
    [CNCFia.kicad_pcb, CNCFia.sch, Level_Shifters.sch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]
2020-02-10 Changed wrong GND for limit switches
    [CNCFia.kicad_pcb, CNCFia.sch, Level_Shifters.sch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]
2020-02-14 New libs and 3d/footprints
    [G6RL_1.step]
2020-02-14 Adds a sheet for pull up resistors on extra sw
    [extra_switches.sch]
2020-02-14 Change mosfets and resistors to arrays
    [CNCFia.kicad_pcb, CNCFia.sch, Level_Shifters.sch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]
2020-02-14 Made it more neat and organized
    [CNCFia.kicad_pcb, CNCFia.sch]
2020-02-14 Fixing Symbols
    [CNCFia.kicad_pcb, CNCFia.sch, Level_Shifters.sch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]
2020-02-14 More symbols fixed
    [opto_limits.sch]
2020-02-14 Simplify the power options
    [CNCFia.kicad_pcb, CNCFia.sch, Relays.sch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]
2020-02-14 Simplify the power options again
    [CNCFia.kicad_pcb, CNCFia.sch]
2020-02-15 Cosmetic and text changes
    [CNCFia.kicad_pcb, CNCFia.sch, Level_Shifters.sch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]

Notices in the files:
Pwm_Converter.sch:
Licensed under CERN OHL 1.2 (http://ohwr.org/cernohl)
